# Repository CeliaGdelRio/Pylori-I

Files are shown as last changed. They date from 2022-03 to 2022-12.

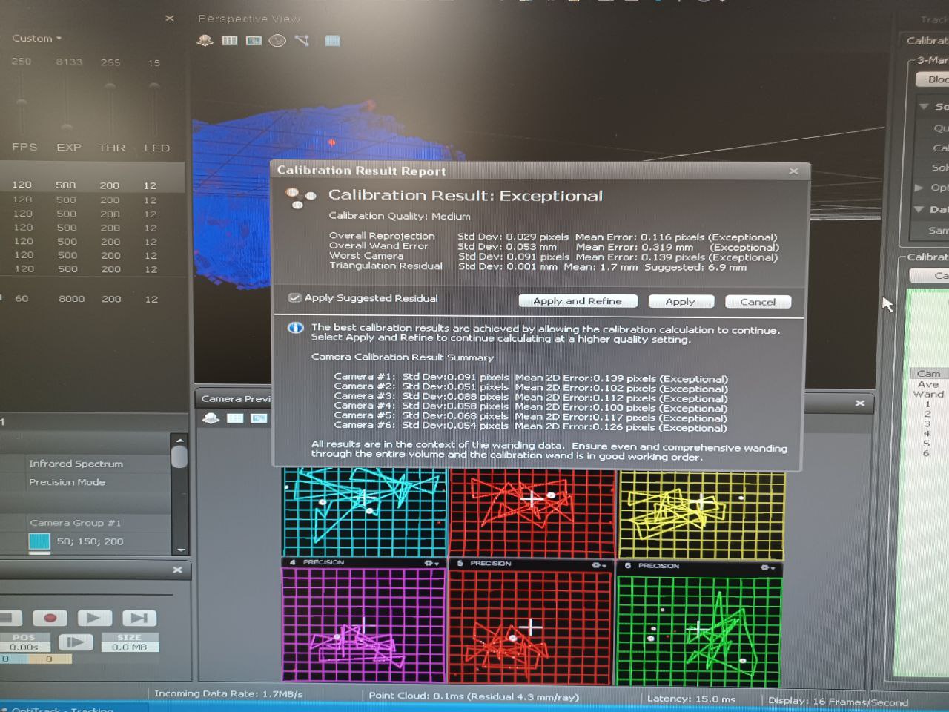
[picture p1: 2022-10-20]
Images/calibracion_final.jpg

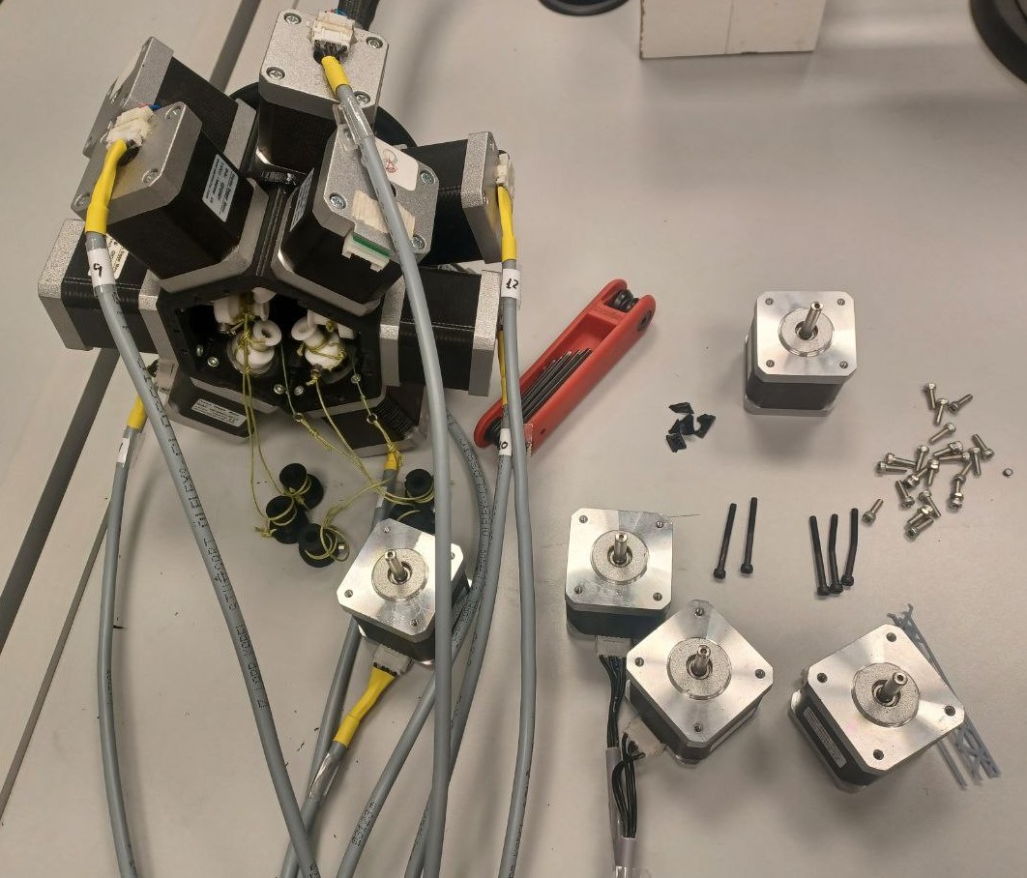
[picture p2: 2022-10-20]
Images/desmontaje.jpg

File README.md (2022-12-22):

# Pylori-I
Hello world!

Este proyecto contiene el código necesario para simular el comportamiento y controlar el movimiento del robot Pylori-I del CAR de la UPM.

Para poder ejecutar este código hay que tener en cuenta varias cosas:
	1. El archivo .ino debe estar cargado en el Arduino Due que contiene el armario. Y de usarse en otro arduino habría además que cargar la librería AccelStepper
	2. El armario debe encenderse correctamente antes de intentar mover el robot: hay que comprobar que el magnetotérmico del interior este subido, la seta de emergencia no esté pulsada y entonces encender el armario.
	3. El código con la cinemática está escrito en MATLAB R2020 o R2021, y el que mueve el robot en MATLAB R2022a, por lo que si se usa en versiones posteriores puede que esté desfasado.
	
### CONTENIDO Y CARPETAS:	

* **Arduino:** Contiene el archivo que debe estar cargado en la placa Arduino Due del armario electrico para poder ejecutar correctamente el código que mueve el robot
* **Images:** Contiene las imagenes que se han empleado para la memoria y algunas mas. Las imagenes que he obtenido de otras fuentes estan debidamente citadas en la memoria TFM_Celia Garijo del Rio.pdf de la carpeta Memorias_TFM. Las demás son de elaboracion propia por lo que se pueden usar citando la memoria (las que aparecen en ella) o este repositorio.
*  **Memorias_TTFM:** Contiene las tres memorias de los trabajos de final de grado o master en los que se ha desarrollado este proyecto.
*  **Red_neuronal:** Contiene el codigo empleado para entrenar las dos redes neuronales en python así como un archivo .csv con los datos que se han empleado en este caso y archivos .txt con las variables (W1, W2, b1, b2, ymin, ymax, xmin y xmax) obtenidas tras entrenar la red que permiten aplicarla en otros programas como Matlab.
*  **Toma de datos:** Contiene el codigo que se ha empleado tanto para la toma de datos del comportamiento del robot como para el tratamiento de datos.
*  **piezas_STL:** Contiene todos los archivos .stl de las piezas mecanicas que se han diseñado para el robot. Para poder ejecutar el codigo que mueve el robot es necesario tener en la misma carpeta los archivos Robot_Base.stl, End_Boro_Triang.stl y Mod_Boro_Triang.stl.

El codigo que queda fuera de las carpetas es el que se emplea para mover el robot y el que contiene la cinematica. A continuacion se describe en mas detalle como usar este ultimo.

### CÓMO SE USA ESTE CÓDIGO:

**IMPORTANTE:** Se ha incluido un archivo .cff en este repositorio para que resulte más sencillo citar este repositorio a quien lo pueda necesitar.

Las funciones Demo y Demo_Trayectorias sirven para simular la cinemática del robot cuando se mueve a un punto (definido en caartesianas), en el caso de Demo, o traza una trayectoria pasando por varios puntos (también en cartesianas), en el caso de Demo_trayectorias; y devuelven los datos necesarios para mover el robot hasta ese punto o trazar esa trayectoria mediante la función moverRobot.
	
**IMPORTANTE:** antes de empezar a ejecutar cualquier función que se comunique con Arduino (moverRobot, calibrarRobot, mover_motor) hay que abrir la conexión con Arduino como se muestra a continuación:
		
```matlab
ardu=serialport("COM3",250000);
```
		
donde "COM3" se deve sustituir por el puerto que esté ocupando Arduino. Y lo primero que hay que hacer después de establecer la conexión es establecer la posición actual como la inicial:
		
```matlab
calibrarRobot(ardu,0,1);
```	
		
Esta conexión no se debe cerrar hasta que no se haya terminado de mover el robot o se perderá los datos sobre cual es la posición inicial. Antes de cerrar se devuelve el robot a la posición inicial y despues se cierra la conexión borrando el objeto ardu:
```matlab
calibrarRobot(ardu,2,1);
delete(ardu);
```

Una vez abierta la conexión y establecida la posición inicial, las formas de mover el robot son las siguientes:
 	
* Para mover motor a motor (mediante la función mover_motor). 
	* Si se quiere mover motor m hasta la posición pos(en pulsos) a la velocidad vel (en pulsos/s):
	```matlab
	mover_motor(ardu,m,2,vel,pos,1);
	```
	* Si se quiere mover motor m a la velocidad vel (en pulsos/s) durante s segundos:
	```matlab
	mover_motor(ardu,m,1,vel,0,s);
	```
* Para moverlo a un punto (x,y,z):
```matlab
[newConfig,error,iter,currentPos]=Demo(x,y,z);
moverRobot(ardu,newConfig,0,1);
```
Donde el 0 en el tercer argumento de moverRobot indica que es un punto y no una trayectoria y el cuarto argumento indica que es un solo punto. Además, la variable error da el error que se espera de la simulación, la variable iter, el nº de iteraciones que ha tenido que hacer la simulación.

* Para llevar el robot a la posición inicial:
```matlab
calibrarRobot(ardu,2,1);
```
* Para establecer la posición actual como la inicial:
```matlab
calibrarRobot(ardu,0,1); 	
```

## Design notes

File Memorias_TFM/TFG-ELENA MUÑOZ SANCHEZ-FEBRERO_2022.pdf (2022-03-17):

# CONSTRUCCIÓN Y CONTROL DE UN ROBOT CONTINUO DE CABLES CON

# DISCOS PIVOTANTES

FEBRERO 2022

# Elena Muñoz Sánchez

DIRECTOR DEL TRABAJO FIN DE GRADO:

## Antonio Barrientos Cruz

## Elena Muñoz Sánchez

### TRABAJO FIN DE GRADOPARA LA OBTENCIÓN DEL TÍTULO DE GRADUADO EN INGENIERÍA EN TECNOLOGÍAS INDUSTRIALES

“Más vale tarde que nunca”

“Algún día diré: No fue fácil, pero lo logré”

ELENA MUÑOZ SÁNCHEZ | V

AGRADECIMIENTOS

En primer lugar, quiero agradecer a mi familia su apoyo y amor incondicional durante estos largos años. Sin vosotros no estaría donde estoy ni habría llegado a ser quien soy ahora.

A mi tutor, Antonio, por creer en mí a lo largo de todo el proyecto más que yo misma, y apoyarme en todas las dudas e impedimentos que me he ido encontrando.

A mis dos grandes mentores, Iván y David, por mostrarme este proyecto y guiarme siempre que lo he necesitado.

A mi compañero Jaime, por ayudarme a materializar el Pylori-I y aguantarme en los peores momentos.

A la asociación de estudiantes RESET, por todo lo que me ha aportado estos últimos años, tanto académica como profesionalmente.

Y a todos los que me habéis acompañado durante esta etapa, en especial a La Taca, a Laura y a Elisa, por compartir esta aventura y levantarme siempre que me caía.

CONSTRUCCIÓN Y CONTROL DE UN ROBOT CONTINUO DE CABLES CON DISCOS PIVOTANTES

ELENA MUÑOZ SÁNCHEZ | VII

RESUMEN

Los robots híper-redundantes son aquellos que poseen un gran número de grados de libertad en comparación con los robots convencionales. La complejidad de su diseño y de su control hacen que su uso no sea tan frecuente como el de los robots no redundantes. Sin embargo, en determinadas aplicaciones, como por ejemplo aquellos casos en los que se hace necesario un elevado grado de maniobrabilidad para trabajar en espacios muy confinados, su uso es casi imprescindible.

El uso de robots híper-redundantes permite resolver con éxito ciertas tareas de inspección o incluso mantenimiento en entornos industriales, aeroespacial, seguridad y vigilancia, y medicina, que serían inabordables con cinemáticas de robots más convencionales.

En este proyecto, se ha diseñado y construido el robot llamado Pylori-I. Se trata de un manipulador continuo híper-redundante que consta de 16 grados de libertad (GdL) distribuidos de cuatro en cuatro a lo largo de sus cuatro secciones. Tiene una longitud de 260 mm a los que se suman otros 48 mm del distribuidor de cables y 155 mm del banco de motores, haciendo un total de 463 mm. La estructura está formada por discos impresos en 3D que pivotan unos sobre otros siguiendo la construcción de robots con twin-pivot compliant joints (TPCJ) y que son accionados mediante motores paso a paso con transmisión por cables.

En su desarrollo, se ha partido del robot desarrollado por Iván Rodríguez en su Trabajo de Fin de Máster [1] y del diseño de endoscopios médicos [2], rediseñando y modificando determinados aspectos para poder llevar a cabo su materialización.

Se trata de un diseño innovador que busca prescindir del empleo del denominado backbone o núcleo central con el que cuentan la mayor parte de los robots híper-redundantes, liberando así el espacio central del robot y aligerando su peso, sin perder sus capacidades de maniobrabilidad que le dotan de gran versatilidad y flexibilidad.

Con este robot se pretende realizar tareas que requieran accesos complicados para el ser humano, como la inspección o el mantenimiento en el interior de máquinas o tuberías, o que sean peligrosas, como la inspección de lugares donde puedan ocultarse explosivos u otro tipo de amenazas. Otra de las principales aplicaciones buscadas, es su empleo en la medicina debido a su pequeño diámetro, lo cual permitiría también realizar inspecciones visuales si se redujera más su tamaño, comportándose como un endoscopio.

Durante el desarrollo del trabajo, se ha realizado un primer estudio del movimiento del robot en Matlab, obteniendo una simulación precisa de su comportamiento. Se han implementado nuevas restricciones, detección de colisiones, cálculo de trayectorias y del espacio de trabajo y estimación de las elongaciones necesarias para los cables. Tras ello, se han rediseñado y fabricado los elementos constitutivos del robot y se ha procedido a su montaje, manteniendo requisitos de posible reconfiguración. Se ha puesto en marcha el sistema de accionamiento basado en motores paso a paso (PaP) y su control mediante Arduino. También se ha diseñado un sistema de calibración y medida buscando facilitar estas tareas habitualmente problemáticas en los robots de cables. Finalmente, se han llevadlo a cabo una serie de experimentos para evaluar la calidad de su posicionamiento.

Los experimentos realizados han permitido obtener una serie de conclusiones y detectar posibles futuras líneas de investigación.

Se espera que este robot suponga un avance en el campo de la robótica híper-redundante y continua que utiliza TPCJ.

RESUMEN

VIII | ESCUELA TÉCNICA SUPERIOR DE INGENIEROS INDUSTRIALES (UPM)

CONSTRUCCIÓN Y CONTROL DE UN ROBOT CONTINUO DE CABLES CON DISCOS PIVOTANTES

ELENA MUÑOZ SÁNCHEZ | IX

ABSTRACT

Hyper-redundant robots are those that have many more degrees of freedom compared to conventional robots. The complexity of its design and control means that its use is not as frequent as that of non-redundant robots, but in certain applications, such as those cases in which a high degree of manoeuvrability is necessary to work in very small spaces, its use is almost essential.

The use of hyper-redundant robots makes it possible to successfully solve certain inspection or even maintenance tasks in industrial, aerospace, security and surveillance, and medical environments, which would be intractable with conventional robot kinematics.

In this project, a robot named Pylori-I has been designed and built. It is a hyper-redundant continuous manipulator consisting of 16 degrees of freedom (DoFs) distributed four by four along its four sections. It has a length of 260 mm to which another 48 mm of the cable distributor and 155 mm of the engine bank are added, making a total of 463 mm. The structure is made up of 3D printed disks that pivot on each other following the construction of robots with twin-pivot compliant joints (TPCJ), and that are driven by stepper motors with cable transmission.

In its development, it has been based on the robot developed by Iván Rodríguez in his master’s Thesis [1] and the design of medical endoscopes [2], redesigning and modifying certain aspects in order to carry out its materialization.

It is an innovative design that seeks to dispense with the use of the so-called backbone or central core that most hyper-redundant robots have, thus freeing up the central space of the robot and lightening its weight, without losing its manoeuvrability capabilities, which give great versatility and flexibility.

This robot is intended to perform tasks that require difficult access for humans, such as inspection or maintenance inside machines or pipes, or that are dangerous, such as inspection of places where explosives or other types of threats may be hidden. Another of the main applications sought is its use in medicine due to its small diameter, which would also allow visual inspections if its size were further reduced, behaving like an endoscope.

During the development of the project, a first study of the robot's movement has been carried out in Matlab, obtaining an accurate simulation of its behaviour. New restrictions, collision detection, calculation of trajectories and workspaces, and estimation of the necessary elongations for the cables have been implemented. Later, the constituent elements of the robot have been redesigned and manufactured and its assembly has proceeded, maintaining the possible reconfiguration requirements. The drive system based on stepper motors (PaP) and its control through Arduino have been launched. A calibration and measurement system has been designed, seeking to facilitate these tasks, which are usually problematic in driven tendons robots. Finally, a series of experiments have been carried out to evaluate the quality of its positioning.

The experiments carried out have made possible to obtain a series of conclusions and to detect possible future lines of research.

This robot is expected to be a breakthrough in the field of hyper-redundant and continuous robotics using TPCJ.

ABSTRACT

X | ESCUELA TÉCNICA SUPERIOR DE INGENIEROS INDUSTRIALES (UPM)

CONSTRUCCIÓN Y CONTROL DE UN ROBOT CONTINUO DE CABLES CON DISCOS PIVOTANTES

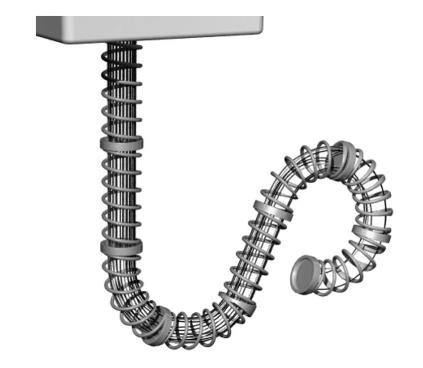
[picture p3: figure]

ELENA MUÑOZ SÁNCHEZ | XI

RESUMEN EJECUTIVO

Actualmente, se puede encontrar una gran variedad de tipos de robots, pero en este trabajo se estudiará el caso del Pylori-I, un robot híper-redundante, continuo y blando construido mediante discos pivotantes y accionado por cables y motores paso a paso.

Un robot híper-redundante es aquel que posee un número de grados de libertad igual o superior al doble del número de dimensiones del espacio de trabajo. De esta manera, este tipo de robots están dotados de una flexibilidad y maniobrabilidad mayores que las de los robots convencionales.

Ilustración 1. Prototipo de robot continuo e híper-redundante. Fuente: http://www.ccad.uiowa.edu/sites/www.ccad.uiowa.edu.vsr/files/files/Continuum-Robot-AR.pdf

Los robots de tipo continuo son aquellos que no están formados por uniones rígidas, lo cual provoca que el robot se deforme de manera continuada y natural, de ahí su nombre.

En el caso de los robots de tipo blando (soft robots), se denominan de esta manera debido a que los materiales que los componen no generan una estructura rígida que pueda causar daños en su entorno. Es por ello por lo que pueden emplearse como robots colaborativos o instrumentos médicos.

A pesar de que una de las funcionalidades principales de los robots híper-redundantes es la inspección visual de zonas poco accesibles, este trabajo se ha centrado en el desarrollo de un robot que se asemeje a un endoscopio y que permita su aplicación en áreas de la cirugía poco invasiva en distintas especialidades médicas y quirúrgicas.

Para el diseño del Pylori-I se han comparado diferentes prototipos estudiados previamente en el Centro de Automática y Robótica, como el Kyma o el MACH-I. Finalmente, se ha decidido implementar el método de construcción que emplea twin-pivot compliant joints.

Para su construcción, se han impreso en 3D la mayor parte de los componentes con la colaboración de la asociación de estudiantes RESET. Los motores e hilos se han tenido que comprar externamente.

RESUMEN EJECUTIVO

XII | ESCUELA TÉCNICA SUPERIOR DE INGENIEROS INDUSTRIALES (UPM)

Para la colocación del robot en posición horizontal, se ha diseñado un soporte ad hoc adaptado a los espacios libres que dejan los motores.

Ilustración 2. Pylori-I conectado al armario eléctrico y colocado horizontalmente sobre el soporte

La actuación mediante cables se ha dividido en dos fases que utilizan un tipo de cable diferente. Aunque ambos son hilos de pesca, el más grueso se colocará en la polea, ya que va a ser el cable que más sufra de los dos, enrollándose y desarrollándose continuamente. Además, el banco de motores es extrínseco al cuerpo del robot, por lo que aligerará en gran medida el peso del brazo robótico.

Ilustración 3. Cables usados para la actuación. Fuente: https://www.amazon.es/

En cuanto a la construcción del brazo robótico, la estructura está formada por apilamientos de discos que forman secciones siguiendo una distribución 20-12-12-8 partiendo desde la base.

Cada una de las secciones tiene como disco final una modificación de los anteriores para poder alojar el final de los cables en su cara lateral. Además, estas secciones se encuentran desfasadas 2π/16 radianes entre sí y están actuadas cada una de ellas por cuatro cables diametralmente opuestos dos a dos.

Esta configuración de los cables ha sido estudiada en el trabajo, resultando ser la que menores tensiones genera.

CONSTRUCCIÓN Y CONTROL DE UN ROBOT CONTINUO DE CABLES CON DISCOS PIVOTANTES

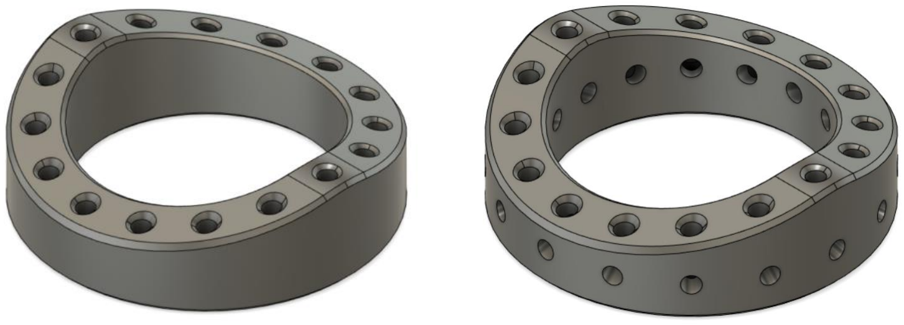
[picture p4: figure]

ELENA MUÑOZ SÁNCHEZ | XIII

Ilustración 4. Discos utilizados en la construcción de las secciones

En total, se obtienen 16 grados de libertad para todo el robot, cuatro por sección, quedando como diseño final el siguiente:

Ilustración 5. Diseño final del Pylori-I realizado con Catia V5

En cuanto al control cinemático del robot, se ha hecho un estudio y comparación de tres cinemáticas existentes, descartando aquellas que utilizan el método de cálculo de la matriz Jacobiana.

Una vez determinado cómo se va a generar el movimiento del Pylori-I, se han implementado nuevos métodos y funciones en Matlab que serán utilizados para el posicionamiento del extremo, la generación de trayectorias, la detección de colisiones, el cálculo de las elongaciones de cada uno de los cables y la estimación de las dimensiones del espacio de trabajo.

También mediante Matlab, se ha creado una interfaz hombre-máquina dentro de la cual se podrá activar la conexión Matlab-Arduino, ver el número total de colisiones ocasionadas y los discos implicados en las mismas y, lo más importante, introducir coordenadas que generen la simulación de posicionamiento del extremo.

Esta interfaz también mostrará la posición real en la que se ha situado el Tool Center Point y el error generado en el posicionamiento.

RESUMEN EJECUTIVO

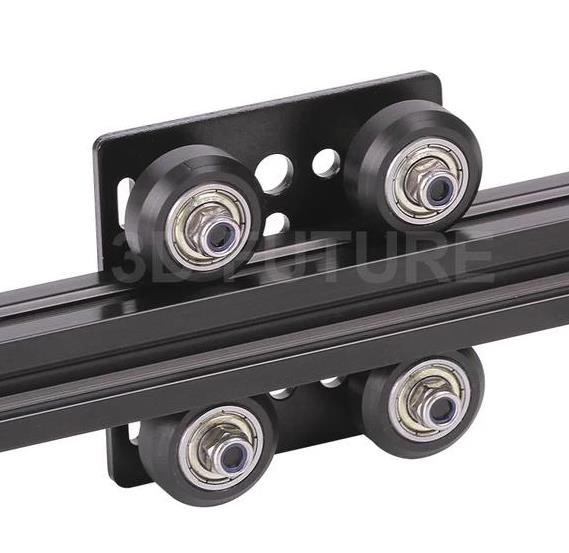
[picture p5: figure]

XIV | ESCUELA TÉCNICA SUPERIOR DE INGENIEROS INDUSTRIALES (UPM)

Ilustración 6. Pantalla principal de la interfaz

En lo referido al hardware de control, se han utilizado motores paso a paso NEMA17 cuyo conexionado se ha realizado a través de un armario eléctrico proporcionado por el Centro de Automática y Robótica.

Este armario está compuesto por 18 drivers de tipo TB6600 y un Arduino Due. Las dos conexiones sobrantes del armario permitirán en un futuro conectar motores que se encarguen del manejo de una herramienta colocada en el extremo del robot.

Los drivers están configurados para que cada motor de 200 pasos/rev tenga un microstepping que los transforme en 1600 pulsos por revolución.

Una vez iniciado el puerto Serial de Arduino, se enviarán a la placa los pulsos calculados por Matlab para cada uno de los motores siguiendo esta sintaxis:

[Motor;Comando;Arg1;Arg2;]

Para la realización de experimentos se ha construido un espacio físico de trabajo para poder realizar medidas de calibración y de posicionamiento.

El conjunto del espacio de trabajo está formado por perfiles de aluminio, carros V-Slot, piezas impresas en 3D y láseres.

Ilustración 7. Ejemplo de carro V-Slot

CONSTRUCCIÓN Y CONTROL DE UN ROBOT CONTINUO DE CABLES CON DISCOS PIVOTANTES

ELENA MUÑOZ SÁNCHEZ | XV

La calibración del robot se realiza a través de Matlab con la siguiente función en los modos ‘0’ y ‘1’:

function calibrarArduino(Arduino,modo,motor,pul);

El modo ‘0’ guarda la posición actual de cada uno de los motores como la posición de reposo. El modo ‘1’ sirve para enviar un número de pulsos a un motor concreto, realizando de esta manera, poco a poco, una calibración de cada uno de los motores hasta que el robot se encuentre alineado con los láseres lineares fijos de los perfiles.

Los experimentos realizados se han centrado en la medición de las coordenadas de la posición final del extremo del robot calculada de forma directa o mediante la generación de una trayectoria. Además, se han generado trayectorias con diferente número de puntos intermedios para enriquecer el estudio y la discusión posterior.

Una vez analizados los datos obtenidos, se puede concluir que el error de posicionamiento producido en la generación de trayectorias es menor que en el posicionamiento directo. Sin embargo, no se aprecia una influencia significativa del número de puntos intermedios de las trayectorias.

Como posibles futuras líneas de investigación para este proyecto se han propuesto la mejora de la interfaz, la reconstrucción con materiales más fiables y que generen menos rozamiento, la instalación de una herramienta en el extremo del robot, ya sea una pinza o una cámara para inspección, el diseño de un método de calibración y de medición más fiable y preciso, y la implementación de un control mediante joystick o realidad virtual.

La conclusión principal obtenida de la realización de este proyecto es que se observan diferencias entre el comportamiento del robot físico y los obtenidos de manera teórica, lo cual puede deberse a que se ha considerado un comportamiento ideal para el robot (la flexión de la sección se distribuye uniformemente a lo largo de todos los discos que la conforman), a la fricción entre cables y discos, a una mala calibración inicial o a la pérdida de ésta según se avanza con las pruebas.
Sin embargo, hay que destacar que el comportamiento del robot no es del todo erróneo ya que se orienta y aproxima hacia el punto deseado y, pese a que se trata del primer prototipo realizado en el Centro de Automática y Robótica que emplea twin-pivot compliant joints como método constructivo, el Pylori-I posee todas las características buscadas para tener una gran flexibilidad y maniobrabilidad.

Información accesible:

Repositorio:
https://github.com/LnaMzSz/Pylori-I
Lista de reproducción:
https://youtube.com/playlist?list=PL3Q5Xz4yvA3jVhCCdIYIbSSO-qLm97V_n

Palabras clave:

Automática, automatización, continuo, control, híper-redundante, manipulador, robot, robótica, simulación.

RESUMEN EJECUTIVO

XVI | ESCUELA TÉCNICA SUPERIOR DE INGENIEROS INDUSTRIALES (UPM)

Códigos UNESCO:

120326 – Simulación

330491 – Robótica

331101 – Tecnología de la automatización

331102 – Ingeniería de control

CONSTRUCCIÓN Y CONTROL DE UN ROBOT CONTINUO DE CABLES CON DISCOS PIVOTANTES

ELENA MUÑOZ SÁNCHEZ | XVII

ÍNDICE DE CONTENIDOS

AGRADECIMIENTOS | V
RESUMEN | VII
ABSTRACT | IX
RESUMEN EJECUTIVO | XI
ÍNDICE DE CONTENIDOS | XVII
ÍNDICE DE FIGURAS | XIX
ÍNDICE DE TABLAS | XXI

ÍNDICE DE CONTENIDOS

XVIII | ESCUELA TÉCNICA SUPERIOR DE INGENIEROS INDUSTRIALES (UPM)

CONSTRUCCIÓN Y CONTROL DE UN ROBOT CONTINUO DE CABLES CON DISCOS PIVOTANTES

ELENA MUÑOZ SÁNCHEZ | XIX

ÍNDICE DE FIGURAS

Ilustración 1. Prototipo de robot continuo e híper-redundante. Fuente:
http://www.ccad.uiowa.edu/sites/www.ccad.uiowa.edu.vsr/files/files/Continuum-Robot-AR.pdf | XI
Ilustración 2. Pyltori-I conectado al armario eléctrico y colocado horizontalmente sobre el soporte .... XII
Ilustración 3. Cables usados para la actuación. Fuente: https://www.amazon.es/ | XII
Ilustración 4. Discos utilizados en la construcción de las secciones | XIII
Ilustración 5. Diseño final del Pylori-I realizado con Catia V5 | XIII
Ilustración 6. Pantalla principal de la interfaz | XIV
Ilustración 7. Ejemplo de carro V-Slot | XIV
Ilustración 8. Ejemplo de robot continuo construido mediante twin-pivot compliant joints. Fuente: [3] .. 1

Ilustración 11. Representación en función de su número de GdL en un espacio tridimensional (m=3).
(a) Robot no redundante de tipo n<m. (b) Robot no redundante de tipo n=m. (c) Robot redundante de

Ilustración 12. Ejemplo de robot manipulador móvil. Fuente:

Ilustración 14. Ejemplo de representación de un robot continuo accionado mediante cables. Fuente:

Ilustración 17. Esquema de la construcción de robots continuos. En el caso del uso de TPCJ (a), los

Ilustración 18. Parámetros de la cinemática de robots continuos con backbone y TPCJ. Fuente: [12] 11

Ilustración 20. Robot concéntrico compuesto de un tubo exterior y un tubo guía que alberga la fibra

Ilustración 21. (A) Sistema de robot continuo tubular para cirugía de laringe. (B) Modelo de laringe

Ilustración 26. Bacteria Helicobacter Pylori y robot Pylori-I. Fuente:

Ilustración 36. Bobina de Nylon PA12 Blanco. Fuente: https://www.3djake.es/fiberlogy/nylon-pa12-

Ilustración 40. Malla cubre cables. Fuente: https://computacion.mercadolibre.com.ar/cables-hubs-

ÍNDICE DE FIGURAS

XX | ESCUELA TÉCNICA SUPERIOR DE INGENIEROS INDUSTRIALES (UPM)

Ilustración 45. A la izquierda, Método de la Jacobiana utilizando como variables los ángulos de los discos. A la derecha, Método de la Jacobiana utilizando como variables los ángulos de las secciones

Ilustración 46. Posición real del extremo y error generado con el Método del Descenso del Gradiente.

Ilustración 49. Representación de los ángulos θ, φ y α de la sección. Fuente: Modificado de [17] ...... 32

Ilustración 62. Visión general del espacio de trabajo y posicionamiento del Pylori-I en el mismo ........ 43

CONSTRUCCIÓN Y CONTROL DE UN ROBOT CONTINUO DE CABLES CON DISCOS PIVOTANTES

ELENA MUÑOZ SÁNCHEZ | XXI

ÍNDICE DE TABLAS

ÍNDICE DE TABLAS

XXII | ESCUELA TÉCNICA SUPERIOR DE INGENIEROS INDUSTRIALES (UPM)

# 1. INTRODUCCIÓN

CONSTRUCCIÓN Y CONTROL DE UN ROBOT CONTINUO DE CABLES CON DISCOS PIVOTANTES

ELENA MUÑOZ SÁNCHEZ | 1

### 1. INTRODUCCIÓN

### 1.1. Motivación

La principal motivación para la realización de este proyecto es que se trata de un gran reto tanto mecánico como automático, dada la innovación y la dedicación necesaria.

Ilustración 8. Ejemplo de robot continuo construido mediante twin-pivot compliant joints. Fuente: [3]

Pese a la idea previa de que, quizás, tras su realización, acabara siendo un proyecto poco viable o no funcionara de manera correcta fuera de la simulación por tratarse de un primer prototipo, la posibilidad de adentrarse de esta manera en el campo de la robótica y poner en práctica todos los conocimientos adquiridos durante estos últimos años fue suficiente para seguir adelante.

Por último, ser partícipe de un proyecto tan amplio que involucra tantos campos de la ingeniería y tantas líneas futuras diferentes de investigación y de mejora, ha supuesto adquirir unos conocimientos que, realizando un proyecto más común y conocido, no habría sido posible obtener.

1.1.1. Motivación personal

Por otro lado, la motivación personal que me ha llevado hasta aquí ha sido lo atractiva que era la idea de construir y controlar un tipo de robot diferente de los que ya se han estudiado en otros trabajos de fin de carrera o máster en el Centro de Automática y Robótica (CAR).

También es un orgullo poder retomar un proyecto ideado por un amigo y antiguo alumno y hacerlo real, además de su desarrollo en simulación.

### 1.2. Objetivos

Los objetivos del proyecto se pueden dividir en tres partes:

En primer lugar, realizar un estudio del estado del arte de robots híper-redundantes, e investigar y adquirir los conocimientos necesarios para la adaptación del diseño original y su posterior construcción y control. En concreto, se ha decidido abarcar la posible mejora que puede suponer un robot híper-redundante que no posea un eje flexible central y que sea de tamaño muy reducido.

Para rediseñar los componentes existentes y crear nuevos, será necesario familiarizarse con el uso de programas tanto de diseño 3D, concretamente Catia V5 y Autodesk Fusion 360; como de impresión 3D, Simplify 3D y Prusa Slicer.

INTRODUCCIÓN

2 | ESCUELA TÉCNICA SUPERIOR DE INGENIEROS INDUSTRIALES (UPM)

En segundo lugar, se encuentra el estudio de las cinemáticas existentes del robot mediante Matlab. Para ello, se emplea una simulación que permite contemplar el comportamiento del robot en tres dimensiones dentro de su espacio de trabajo. Además, se añaden nuevas restricciones, así como la detección de colisiones, el cálculo de trayectorias y del espacio de trabajo, la estimación de las elongaciones de los cables y la comunicación Matlab-Arduino.

En tercer y último lugar, se procede con la construcción del robot, el estudio del armario eléctrico proporcionado por el CAR, la realización del control mediante Arduino, y la realización de los experimentos de comprobación del funcionamiento.

Además de todo lo mencionado, se pretende aprender a realizar un Trabajo de Fin de Grado, con la correspondiente adquisición de nuevos conocimientos y capacidades como la planificación temporal o el estudio económico de un proyecto.

### 1.3. Estructura del proyecto

A continuación, se realiza un breve resumen por capítulos de todo el trabajo, excluyendo el capítulo actual, Cap. 1: INTRODUCCIÓN, en el que se han explicado la motivación, los diferentes objetivos buscados, y la siguiente estructura:

- Cap. 2: ESTADO DEL ARTE
Se explicara qué son los robots híper-redundantes, sus principales características, sus clasificaciones, los diferentes tipos de construcción y su similitud con los endoscopios utilizados en medicina.
- Cap. 3: DISEÑO MECÁNICO Y CONSTRUCCIÓN

En este capítulo se realizará una comparación de prototipos y se mostrará el diseño final elegido. Se explicarán las diferentes partes que componen al robot, los rediseños de componentes necesarios y la posterior construcción.
- Cap. 4: CONTROL DE MOVIMIENTO DEL PYLORI-I
En este capítulo se estudiarán las diferentes cinemáticas existentes y se explicarán las funcionalidades programadas para el robot.
- Cap. 5: HARDWARE DE CONTROL
Se hará una descripción de los componentes del armario eléctrico, así como del control realizado con Arduino.
- Cap. 6: EXPERIMENTOS Y RESULTADOS
Se explicará la puesta en marcha del robot, se expondrán los resultados de los experimentos realizados, y se discutirán los posibles fallos y mejoras.
- Cap. 7: LÍNEAS FUTURAS

Tras la discusión de los resultados obtenidos, se estudiarán las posibles mejoras futuras y las nuevas líneas de investigación que se podrían seguir de aquí en adelante.

- Cap. 8: CONCLUSIONES
Una vez realizados los capítulos anteriores, se resumirán en este último todas las conclusiones, tanto positivas como negativas, a las que se haya llegado a lo largo del proyecto.
- ANEXO I: GLOSARIO Y ABREVIATURAS
Se incluirán las definiciones y abreviaturas de las palabras clave del proyecto.

CONSTRUCCIÓN Y CONTROL DE UN ROBOT CONTINUO DE CABLES CON DISCOS PIVOTANTES

ELENA MUÑOZ SÁNCHEZ | 3
- ANEXO II: IMPACTO SOCIAL, AMBIENTAL Y ECONÓMICO

En este anexo, se expondrá un breve estudio del impacto que este proyecto puede llegar a producir en el mundo, tanto medioambientalmente como de manera social y económica.
- ANEXO III: PLANIFICACIÓN TEMPORAL

Se mostrará la planificación temporal a través de un diagrama de Gantt y una Estructura de Descomposición del Proyecto (EDP).
- ANEXO IV: ESTUDIO ECONÓMICO

Por último, se realizará un estudio de los costes totales que ha supuesto la realización de este proyecto.

INTRODUCCIÓN

4 | ESCUELA TÉCNICA SUPERIOR DE INGENIEROS INDUSTRIALES (UPM)

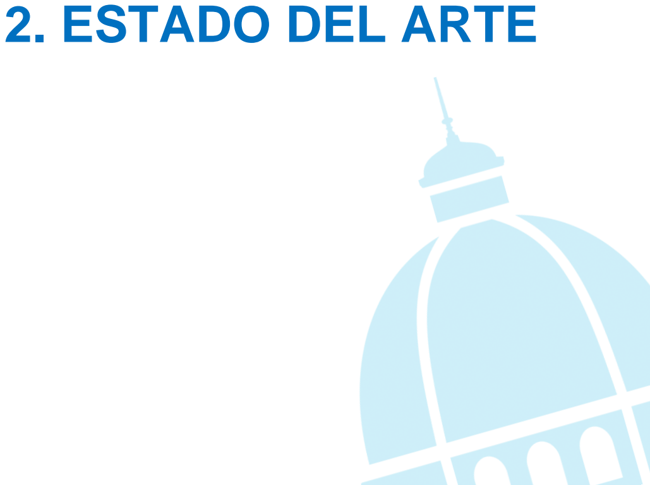
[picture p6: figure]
2. ESTADO DEL ARTE

CONSTRUCCIÓN Y CONTROL DE UN ROBOT CONTINUO DE CABLES CON DISCOS PIVOTANTES

ELENA MUÑOZ SÁNCHEZ | 5

### 2. ESTADO DEL ARTE

### 2.1. Los robots

Existen diferentes definiciones para lo que se conoce como “robot”. Por ejemplo, puede referirse a un objeto que imita comportamientos de un ser animado, una persona que actúa de manera mecánica, o una máquina programable que es capaz de manipular objetos y realizar diferentes tareas.[4] Para este proyecto, la definición más adecuada es la última mencionada.

Por otro lado, el término "híper-redundante", al cual se hará mención muy frecuentemente a lo largo del documento, se refiere a manipuladores con un número muy grande de grados de libertad en comparación con los robots más comunes. Además, se trata de robots que se asemejan bastante a
serpientes, | gusanos, | trompas | de
elefante o tentáculos. [5]

Aunque el proyecto trata de un robot híper-redundante, se va a hacer un estudio de la clasificación general de los robots para más adelante profundizar en el sector que concierne a este trabajo.

### 2.2. Clasificación de los robots

Los robots pueden clasificarse siguiendo cinco características diferentes: según su número de grados de libertad (GdL), según su número de articulaciones, según su funcionalidad, según los materiales con los que se ha construido, y según el tipo de actuación empleada.

Ilustración 10. Diagrama de Venn para la clasificación de los robots. Fuente: [6]

Ilustración 9. Ejemplo de snake-robot. Fuente: https://www.reset.etsii.upm.es/

ESTADO DEL ARTE

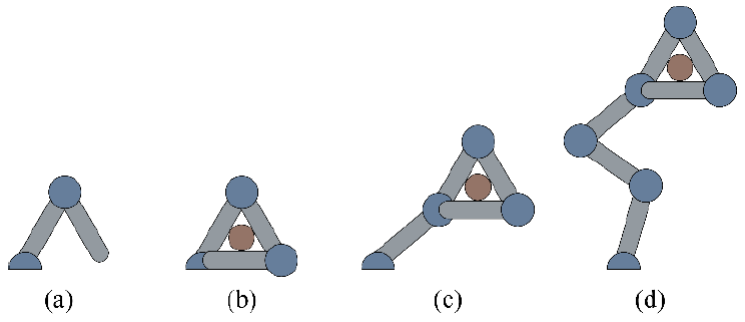
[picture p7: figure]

6 | ESCUELA TÉCNICA SUPERIOR DE INGENIEROS INDUSTRIALES (UPM)
- Según el número de GdL
El número de GdL de un robot es el número de coordenadas independientes que son necesarias para posicionar su extremo respecto a un sistema de referencia dado. [7]

Dentro de esta clasificación se pueden distinguir tres tipos diferentes de robots: no redundantes, redundantes e híper-redundantes.

Siendo m las dimensiones del espacio de trabajo del robot, el número de GdL mínimos necesarios para posicionar su extremo viene dado por la siguiente expresión:

n =

m ∙ (m + 1)
2

De esta manera, se clasificarán como no redundantes aquellos que tengan un número de GdL menor o igual al mínimo necesario; como redundantes aquellos con un número de GdL mayor que el necesario; y como híper-redundantes aquellos que tengan al menos el doble de GdL necesarios.

Ilustración 11. Representación en función de su número de GdL en un espacio tridimensional (m=3). (a) Robot no redundante de tipo n<m. (b) Robot no redundante de tipo n=m. (c) Robot redundante de tipo n>m. (d) Robot híper-redundante de tipo n=2m. Fuente: [6]

- Según el número de articulaciones
Hay que destacar que el término “articulación” no es el mismo que el término “GdL”. Una articulación consiste en una unión entre dos piezas rígidas que permite el movimiento relativo entre ellas. [4]

A su vez, en esta otra clasificación, se diferenciará entre robots continuos y robots discretos.

Los primeros son aquellos que no están formados por uniones rígidas sino por una estructura en la que un único actuador puede transmitir movimiento a más de un eje. Esto provoca que el robot se deforme de manera continuada y natural, de ahí su nombre.

Por otro lado, se denominan robots discretos a aquellos construidos mediante uniones rígidas y perfectamente distinguibles.

- Según su funcionalidad
Atendiendo a la funcionalidad que se tiene como objetivo para el robot, se encuentran dos posibles tipos de robot: manipuladores y móviles.

CONSTRUCCIÓN Y CONTROL DE UN ROBOT CONTINUO DE CABLES CON DISCOS PIVOTANTES

ELENA MUÑOZ SÁNCHEZ | 7

Los robots manipuladores buscan precisión en el posicionamiento del extremo para poder emplear una herramienta que manipule objetos. Además, suelen encontrarse en un espacio de trabajo fijo dentro del cual no se desplazan.

Sin embargo, los robots móviles tienen la capacidad de moverse de un lugar a otro, no teniendo un espacio de trabajo definido.

Cabe la posibilidad de encontrar una mezcla de ambos tipos, los llamados robots híbridos. Estos robots son manipuladores situados en bases móviles, dotando así de locomoción a los primeros. [6]

Ilustración 12. Ejemplo de robot manipulador móvil. Fuente: https://robotnik.eu/es/productos/manipuladores-moviles/

- Según los materiales de construcción
Teniendo en cuenta los materiales utilizados
en la construcción del robot, se diferenciará entre robots duros y robots blandos.

Los robots duros (hard robots) están constituidos por articulaciones rígidas, tratándose así de robots no redundantes generalmente. Por otro lado, los robots blandos (soft robots) tienen una gran adaptación al entorno que les permite sortear objetos con facilidad y pueden ser usados como robots colaborativos dado que están compuestos por materiales blandos que no causarían grandes daños en caso de colisión con una persona. [8]

Como se puede apreciar en la Ilustración 10, los robots de tipo blando están englobados dentro de los robots híper-redundantes y continuos.

- Según el tipo de actuación
Para conseguir un movimiento a lo largo de la estructura del robot, es necesario tener un método de actuación para las articulaciones. Los más utilizados en el caso de robots híper-

Ilustración 13. Ejemplo de robot blando. OctArm VI. Fuente: [6]

ESTADO DEL ARTE

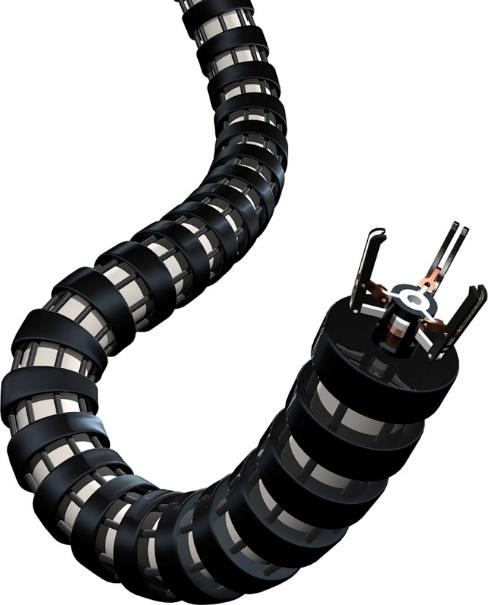
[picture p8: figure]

8 | ESCUELA TÉCNICA SUPERIOR DE INGENIEROS INDUSTRIALES (UPM)

redundantes son el accionamiento mediante cables, las articulaciones motorizadas y la actuación neumática. [1]

El accionamiento por cables permite transferir movimiento a zonas concretas del robot mediante la aplicación de tensión, dotando a la estructura de un movimiento continuo y natural.

Para generar dicha tensión, se emplean motores eléctricos situados en una base extrínseca al brazo robótico, lo cual permite reducir en gran cantidad el peso de éste.

Por otro lado, las articulaciones motorizadas sí forman parte del cuerpo del robot ya que, por lo general, los motores se colocan en las propias articulaciones. Se evita la utilización de elementos de actuación, pero se incrementa en gran medida el peso del robot, lo cual no resulta viable para la construcción.

Por último, hay que destacar que la actuación neumática tiene muchas aplicaciones y es comúnmente utilizada en robots blandos debido a que el aire comprimido no proporciona una estructura rígida por completo. Al igual que en la actuación por cables, se trabaja de forma extrínseca al brazo robótico, pero la dificultad de control es mayor a causa de la regulación de las presiones.

La actuación por cables y por aire comprimido son las más empleadas en robots híper-redundantes, como ya se ha mencionado, debido a sus numerosas ventajas: reducción del peso del robot, trabajo de manera extrínseca, dotación de un movimiento continuo y natural, semejanza con elementos biológicos que evita impactos ambientales, y posibilidad de funcionar como robots colaborativos.

### 2.3. Robots híper-redundantes actuados mediante cables

Como ya se ha mencionado anteriormente, el Pylori-I es un robot híper-redundante continuo actuado mediante cables y motores paso a paso (PaP). Como referencia de estudio, se han tenido soluciones anteriores realizadas en el CAR y que han servido para fijar los objetivos de este trabajo.

Ilustración 14. Ejemplo de representación de un robot continuo accionado mediante cables. Fuente: [2]

La actuación mediante cables es uno de los principios de actuación más destacados para los robots continuos como ya se ha comentado anteriormente. Hasta la fecha, se ha derivado una amplia variedad de enfoques de modelado para describir las deformaciones de los robots continuos accionados por cables.

CONSTRUCCIÓN Y CONTROL DE UN ROBOT CONTINUO DE CABLES CON DISCOS PIVOTANTES

ELENA MUÑOZ SÁNCHEZ | 9
2.3.1. Soluciones previas en el CAR
- Kyma
Consiste en un robot de tipo blando y continuo desarrollado por Cecilia Martínez en 2017 [9]. Está construido con fuelles que proporcionan tres GdL por sección, con un total de cuatro secciones.

Ilustración 15. Robot Kyma (‘onda’ en griego). Fuente: [9]

El accionamiento de este robot se realiza mediante cables y motores PaP conectados entre sí mediante poleas.

- MACH-I
Se trata de un robot inspirado en la trompa de un elefante. Fue diseñado y desarrollado inicialmente por Iván Rodríguez en 2019 [1] y continuado más adelante por David Márquez en 2021 [10].

Es un robot híper-redundante actuado por cables, pero al contrario que ocurría con el robot Kyma, el MACH-I se clasifica como robot duro y discreto.

Ilustración 16. Robot MACH-I. Fuente: [10]

ESTADO DEL ARTE

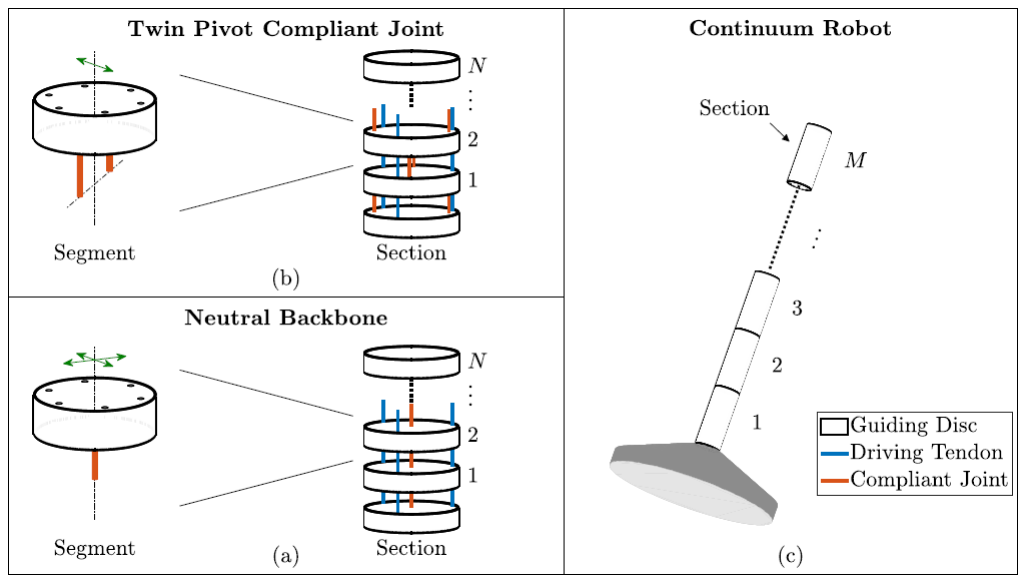
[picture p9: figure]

10 | ESCUELA TÉCNICA SUPERIOR DE INGENIEROS INDUSTRIALES (UPM)

Consta de siete articulaciones con dos GdL por cada una, lo que le confiere su cualidad de robot híper-redundante. Además, cuenta con tres GdL adicionales para actuar sobre una herramienta situada en su extremo.

2.3.2. Backbone vs. twin-pivot complaint joints

En este proyecto, se va a profundizar en la utilización de pivotes en las uniones en lugar de la unión mediante eje flexible o rótulas, lo cual se considera una innovación debido a que no se ha desarrollado ningún robot de este tipo previamente en el CAR. A continuación, se hace un breve estudio y comparación de la información que se tiene respecto a ambas soluciones.

La unidad básica de un robot continuo accionado por cables es el denominado “segmento”. Un segmento es en un componente rígido, llamado disco, junto con un cuerpo elástico, conocido como backbone. [11]

El objetivo de cada uno de los discos que componen la estructura es guiar los cables a través de ésta hasta el extremo de la sección correspondiente, y actuar como limitación de movimiento de la backbone.

Por otro lado, la función del eje flexible (backbone) es dotar al robot de la capacidad de adaptación a diferentes posiciones.

El método utilizado más comúnmente es aquel que utiliza un eje flexible colocado en el eje neutral de los discos del brazo robótico, pero conlleva un gran inconveniente a largo plazo. Este eje flexible tiende a sufrir deformaciones, lo cual provoca la pérdida de control de movimientos de los sectores finales.

Para resolver dicha desventaja, los robots que emplean twin-pivot complaint joints (TPCJ) cambian el diseño de una backbone por dos elementos elásticos diametralmente opuestos. Esta modificación aporta mayor rigidez torsional y libera el eje central para un posible paso de cables para la conexión de una herramienta en el Tool Center Point (TCP). [12]

El montaje que emplea TPCJ, a diferencia de lo que ocurre con un eje flexible, limita los GdL del segmento a uno solo, siendo el eje de flexión del disco el perpendicular al generado por los dos pivotes.

Ilustración 17. Esquema de la construcción de robots continuos. En el caso del uso de TPCJ (a), los segmentos están desfasados alternativamente π/2. Fuente: [12]

CONSTRUCCIÓN Y CONTROL DE UN ROBOT CONTINUO DE CABLES CON DISCOS PIVOTANTES

ELENA MUÑOZ SÁNCHEZ | 11

Una vez apilados N discos, se obtiene la denominada “sección” de un robot. Cada sección está actuada por tres o cuatro cables generalmente, en el caso del Pylori-I, se utilizarán cuatro cables actuadores.

Cada uno de los discos pertenecientes a una sección están vinculados cinéticamente entre sí y actuados por los mismos cables. De manera ideal, que es la que se ha considerado en el desarrollo de este proyecto, la flexión de la sección se distribuirá uniformemente a lo largo de todos los discos que la conforman.

Cabe destacar que el número total de GdL del robot en el caso de utilización de TPCJ, viene dado por el apilamiento de discos con un solo GdL desfasados π/2 entre sí, de tal forma que se obtengan dos GdL por sección, asemejándose así al uso de backbone.

Ilustración 18. Parámetros de la cinemática de robots continuos con backbone y TPCJ. Fuente: [12]

Por último, llegada la hora de la construcción del prototipo, se ha de tener en cuenta que los actuadores de las últimas secciones tienen que pasar a través de las anteriores. Como los cables de las últimas secciones no pueden pasar por las mismas guías que los anteriores, la solución es un desplazamiento angular δ en torno al eje central de los discos para cada sección.

### 2.4. El endoscopio

Los robots continuos son delgados y blandos, y se caracterizan por su alta flexibilidad y su fácil miniaturización. Estas ventajas de las que disponen permiten su aplicación en áreas como la inspección o la cirugía poco invasiva en distintas especialidades médicas y quirúrgicas (neumología, otorrinolaringología, cardiología, aparato digestivo, cirugía general y neurocirugía entre otras). [2]

El endoscopio es un dispositivo médico con una luz incluida creado para poder adentrarse dentro de una cavidad u órgano corporal y observarla. Los procedimientos médicos que utilizan estos instrumentos se denominan “endoscopias”. [13]

2.4.1. Endoscopios robotizados

A continuación, se van a exponer diferentes escenarios en los que se han empleado robots similares al Pylori-I que han sido desarrollados hasta el punto de aplicación en áreas médicas del día a día.

En el área de la neumología, este tipo de robots se han empleado en la toma de muestras de tejido pulmonar a través de bronquios distales de pequeño calibre. [14] Cuanto mayor es la miniaturización de estos endoscopios robotizados, menor será el calibre de los bronquios a los que se puede llegar a acceder con ellos.

ESTADO DEL ARTE

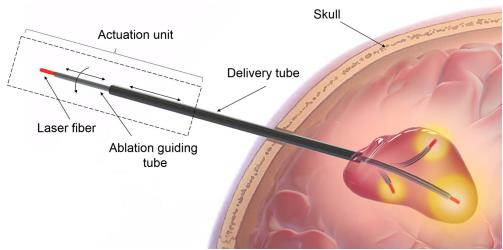
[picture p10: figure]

12 | ESCUELA TÉCNICA SUPERIOR DE INGENIEROS INDUSTRIALES (UPM)

Ilustración 19. Esquema de broncoscopia pulmonar. Fuente: [14]

Este tipo de muestreo pulmonar en pacientes con enfermedades pulmonares como la COVID-19 no está estandarizado, carece de reproducibilidad y requiere operadores expertos. Para ello se propone este tipo de endoscopio (broncoscopio) robotizado que supera los desafíos más importantes a la hora de realizar una broncoscopia, como pueden ser la destreza limitada o el gran tamaño de un broncoscopio convencional. [14]

Dentro del área de la neurocirugía, se puede destacar la termoterapia inducida por láser en el cerebro. Se trata de un procedimiento mínimamente invasivo para acabar con el tejido tumoral.

Dado que los tumores cerebrales de forma irregular no pueden tratarse utilizando los sistemas existentes, se ha presentado un sistema robótico de tubos concéntricos para el tratamiento de éstos. [15]

Ilustración 20. Robot concéntrico compuesto de un tubo exterior y un tubo guía que alberga la fibra láser (roja). Fuente: [15]

CONSTRUCCIÓN Y CONTROL DE UN ROBOT CONTINUO DE CABLES CON DISCOS PIVOTANTES

ELENA MUÑOZ SÁNCHEZ | 13

Por último, en el caso de la otorrinolaringología, se han realizado estudios en modelos de laringes porcinas para evaluar la factibilidad de cirugías transorales con este tipo de robot teleoperado. [16]

La cirugía transoral asistida por robot es cada vez más común lo que conlleva grandes avances en esta área. Sin embargo, los sistemas actuales son incapaces de profundizar lo suficiente como para alcanzar áreas subglóticas.

Ilustración 21. (A) Sistema de robot continuo tubular para cirugía de laringe. (B) Modelo de laringe porcina siendo visualizado mediante endoscopia. Fuente: [16]

ESTADO DEL ARTE

14 | ESCUELA TÉCNICA SUPERIOR DE INGENIEROS INDUSTRIALES (UPM)

# 3. DISEÑO MECÁNICO Y

CONSTRUCCIÓN Y CONTROL DE UN ROBOT CONTINUO DE CABLES CON DISCOS PIVOTANTES

ELENA MUÑOZ SÁNCHEZ | 15

### 3. DISEÑO MECÁNICO Y CONSTRUCCIÓN

### 3.1. Generalidades

Como objetivo principal, se quiere diseñar un robot híper-redundante accionado mediante cables partiendo de las experiencias anteriores en el CAR con robots como Kyma y MACH-I, pero buscando un tipo diferente de robot. De manera más concreta, el objetivo es diseñar y construir un robot de menor escala que los mencionados y que, además, no utilice juntas rígidas ni un eje flexible central. De esta manera, se ganará accesibilidad a espacios más estrechos o de difícil inspección.

Además, se desea que la base del robot pueda usarse con diferentes prototipos, por lo que ha de ser un diseño estándar, generalizado y fácilmente desmontable.

Por último, dado que se trata de un primer montaje de un prototipo para su estudio, no es necesario que el robot sea duradero en el tiempo. Por lo que los componentes del robot, tanto del brazo robótico como de la base de motores, se van a fabricar por impresión 3D. De esta manera, se espera que se minimicen los costes dentro de lo posible.

### 3.2. Requisitos del brazo robótico

3.2.1. Sección y longitud

Ambas dimensiones son críticas para el diseño, pues de ellas dependerá el espacio de trabajo del robot. Dado que se parte del diseño del MACH-I, la intención es lograr una longitud y sección más reducidas sin grandes pérdidas en maniobrabilidad.

La longitud está directamente relacionada con la sección y la carga soportada. Si consideramos un brazo robótico de sección reducida y longitud elevada, los esfuerzos que deberán soportar cada una de las articulaciones aumentarán considerablemente debido al propio peso del robot y la carga. De igual manera, si la sección se reduce en exceso, la tensión en los cables aumentará para poder compensar los esfuerzos provocados por la carga.

Como primera aproximación, se considera un diámetro máximo de 30 mm y una longitud de entre 25 y 35 cm.

3.2.2. Utillaje

Se espera que el brazo robótico sea capaz de realizar pequeñas inspecciones y/o manipulaciones. Para ello, se ha tenido en cuenta en los cálculos una capacidad de carga de 100 g equivalente a la sujeción de una cámara espía, unas pinzas, un imán, o cualquier otro posible acople en el extremo del robot.

### 3.3. Diseños conceptuales previos

Estudios previos realizados en el CAR sobre el desarrollo de manipuladores híper-redundantes [1], han identificado dos posibles opciones constructivas para el robot. A continuación, se van a presentar ambas, para después evaluar sus ventajas e inconvenientes y seleccionar así la más adecuada.

El primer diseño es un robot continuo basado en un endoscopio que utiliza articulaciones basadas en el modelo TPCJ. Por otro lado, el segundo prototipo se basa en un núcleo flexible o backbone donde no existen articulaciones localizadas.

DISEÑO MECÁNICO Y CONSTRUCCIÓN

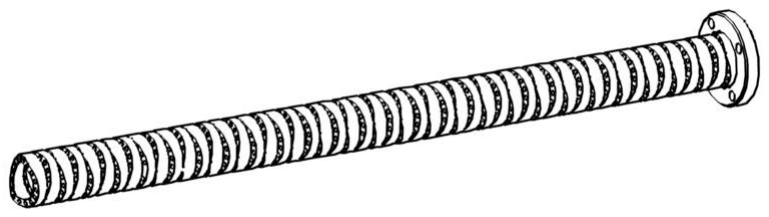
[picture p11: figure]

16 | ESCUELA TÉCNICA SUPERIOR DE INGENIEROS INDUSTRIALES (UPM)
3.3.1. Prototipo 1

El prototipo 1 es un brazo robótico de 17 mm de diámetro y 260 mm de longitud, y es el de construcción más compleja dado el diseño de direccionamiento de los cables.

Ilustración 22. Diseño CAD prototipo 1. Fuente: elaboración propia

Consta de cuatro secciones con una distribución de 20-12-12-8 discos desde la base hacia el extremo. Los discos siguen el modelo TPCJ y están desfasados 90º entre ellos de manera que los ejes de giro de cada sección quedan sin definir.

El accionamiento se realiza mediante
cables que quedan ocultos en el interior del propio
robot. En este diseño son necesarios cuatro
cables por sección debido al desfase mencionado en el párrafo anterior.

El número de secciones viene definido por el número de agujeros para cables que tiene cada disco, en este caso son 16. Si se desea que cada
sección únicamente pueda girar sobre un eje, es
decir, que no exista desfase entre discos, se
emplearían dos cables por sección únicamente y el número de secciones podría duplicarse, llegando a un máximo de ocho.
3.3.2. Prototipo 2

Este modelo tiene una sección de 30 mm y un núcleo flexible de sólo tres milímetros. Está compuesto por siete secciones con tres discos cada una de ellas para proporcionarle una mayor continuidad y, al igual que el prototipo anterior, es accionado mediante cables [1].

Ilustración 24. Diseño CAD prototipo 2. Fuente: [1]

Ilustración 23. Modelo TPCJ y desfase de 90º entre discos

CONSTRUCCIÓN Y CONTROL DE UN ROBOT CONTINUO DE CABLES CON DISCOS PIVOTANTES

ELENA MUÑOZ SÁNCHEZ | 17

Cada disco está formado por dos piezas idénticas atornilladas abrazando el núcleo flexible. En conjunto pueden albergar hasta 36 cables, por lo que, utilizando tres cables por sección, el brazo robótico podría ampliarse hasta un máximo de 12 secciones [1].

Ilustración 25. Disco prototipo 2 y eje flexible. Fuentes: [1] y https://amzn.to/2WA6ahA

El eje flexible posee una gran resistencia a torsión y compresión, pero no hay que olvidar la gran dependencia que supone para el modelo la elasticidad de la que esté dotado el eje.

3.3.3. Comparación de prototipos

A continuación, se exponen brevemente las principales características de ambos prototipos para así, justificar la decisión tomada.

Se trata de dos modelos de robot blando y continuo con un coste de fabricación realmente bajo. A su vez, ambos poseen una baja capacidad de carga, pero como su finalidad son pequeñas inspecciones, para la consideración de una carga máxima de 100 g es suficiente.

Sus diferencias se encuentran en las dimensiones, la facilidad de montaje y el tipo de eje. Pese a la facilidad de montaje del prototipo 2, la disposición de los discos del prototipo 1, su tamaño más reducido y su eje hueco proporcionan mayor libertad de movimiento y precisión. Además, la posibilidad de introducir por el interior el cableado del utillaje, supone una idea innovadora frente al resto de robots construidos con backbone.

### 3.4. Desarrollo

De aquí en adelante, se hará referencia al prototipo 1 como Pylori-I dado su diseño basado en un endoscopio y su gran parecido a la bacteria Helicobacter Pylori.

Ilustración 26. Bacteria Helicobacter Pylori y robot Pylori-I. Fuente: https://cinfasalud.cinfa.com/p/helicobacter-pylori/

DISEÑO MECÁNICO Y CONSTRUCCIÓN

18 | ESCUELA TÉCNICA SUPERIOR DE INGENIEROS INDUSTRIALES (UPM)

Como se ha comentado anteriormente en la comparación de los dos prototipos, este diseño consta de cuatro secciones actuadas por cuatro motores cada una de ellas, es decir, 16 motores en total.
Es posible añadir más secciones si los discos de cada sección se colocan sin desfase entre ellos, de manera que las secciones tengan un único eje de giro máximo.
Para este trabajo, se ha decidido continuar con la distribución planteada inicialmente: cuatro secciones con una distribución de discos de 20-12-12-8 partiendo desde la base. No se ha profundizado en el estudio de una distribución óptima de discos y secciones ya que esto era motivo de estudio de otro trabajo simultáneo [17].
A continuación, se reflejan las principales características del Pylori-I.

Tabla 1. Características del Pylori-I

Para comenzar con el desarrollo, es necesario analizar el caso más desfavorable de análisis de cargas. Estos cálculos servirán más adelante para determinar qué tipo de motor PaP va a emplearse.
La única carga a la que se somete el brazo robótico es su propio peso, aunque se le puede añadir una pequeña carga extra situada en el extremo para futuros utillajes que se puedan instalar. Hacer los cálculos con esta carga adicional nos asegura un margen de
Diámetro exterior del disco (mm) | Øe | 17
Diámetro interior del disco (mm) | Øi | 12
Diámetro de disposición de cables (mm) | Øc | 14.5
Diámetro agujero de cable (mm) | Øa | 0.9
Altura del disco (mm) | H | 4.8 ~ 5
Altura del pivote (mm) | h | 1.7
Desfase entre cables (º) | α | 22.5
Masa del disco (g) | mdisco | 0.49 ~ 0.5
Longitud total (mm) | L | 260
Longitud sección 1 (mm) | L1 | 100
Longitud sección 2 (mm) | L2 | 60
Longitud sección 3 (mm) | L3 | 60
Longitud sección 4 (mm) | L4 | 40
Número de secciones | M | 4
Número total de discos | N | 52
Discos en la sección 1 | N1 | 20
Discos en la sección 2 | N2 | 12
Discos en la sección 3 | N3 | 12
Discos en la sección 4 | N4 | 8
Cables por sección | n | 4
Ángulo máximo de giro del disco (rad) | βmax | 0.23
Ángulo máximo de giro de la sección 1 (rad) | Θ1 | 2.07
Ángulo máximo de giro de la sección 2 (rad) | Θ2 | 1.242
Ángulo máximo de giro de la sección 3 (rad) | Θ3 | 1.242
Ángulo máximo de giro de la sección 4 (rad) | Θ4 | 0.828

CONSTRUCCIÓN Y CONTROL DE UN ROBOT CONTINUO DE CABLES CON DISCOS PIVOTANTES

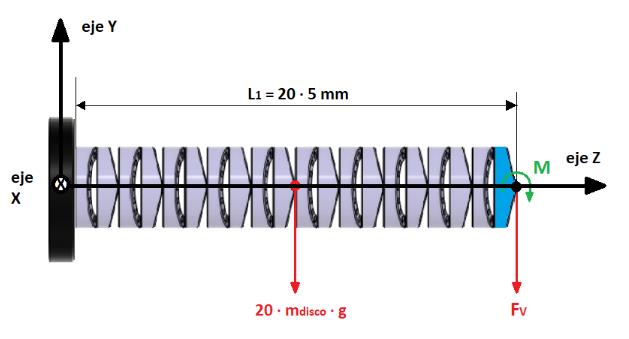
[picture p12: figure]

ELENA MUÑOZ SÁNCHEZ | 19

seguridad a la hora de instalar un utillaje o de manipular con unas pinzas objetos externos al robot que supongan un peso adicional en el extremo.
La carga del extremo se ha fijado en 100 g, que abarca la masa media de un utillaje (30 g los más pesados) más la de un objeto externo de hasta 80 g en algunos casos.
Se conoce el peso de cada disco, cinco gramos, y la altura máxima de los discos, 4.8 mm que se aproximan a cinco milímetros por las rugosidades de las piezas.
El caso más desfavorable se corresponde con la situación en la que el brazo robótico se encuentra en una posición completamente horizontal. En dicha posición el par generado es máximo, pues las masas de las secciones y del extremo se encuentran lo más alejadas posible de la base del brazo.

Ilustración 27. Diagrama de fuerzas en el brazo completo

Las longitudes de las secciones resultan L1 = 100 mm, L2 = 60 mm, L3 = 60 mm y L4 = 40 mm, lo cual implica una longitud total de 260 mm que entra dentro de los requisitos mencionados anteriormente. Sus masas son 10, 6, 6 y 4 gramos respectivamente. Sabiendo que mload = 100 g, suponemos una longitud media de 20 mm para simular el posible utillaje colocado en el extremo.
Partiendo de esta situación, la unión de las secciones 1 y 2 será la zona que soporte más par, por lo que se reduce el análisis a este punto:

Ilustración 28. Reducción de fuerzas

Fv y M son la fuerza y el par que los cables que generan el movimiento deberán compensar. Estos esfuerzos son calculados de la siguiente manera:

Fv = (6 + 6 + 4 + mload) ∙ g ∙ 10⁻3 = 1. 1368 N

DISEÑO MECÁNICO Y CONSTRUCCIÓN

20 | ESCUELA TÉCNICA SUPERIOR DE INGENIEROS INDUSTRIALES (UPM)

M = (6 + 6 + 4 + 1) ∙ 10⁻3

- mload ∙ g + (6 + 6 + 2) ∙ 10⁻3
- 4 ∙ 10⁻3
- g + (6 + 3)
- 10⁻3
- 6 ∙ 10⁻3
- g + 3 ∙ 10⁻3
- 6 ∙ 10⁻3
- g
= 0. 1666 + 0. 0055 + 0. 0053 + 0. 0018 = 0. 1792 N ∙ m

Los cables mencionados antes van a estar distribuidos equitativamente en los discos a lo largo de una circunferencia de 14.5 mm de diámetro y paralelamente al eje longitudinal del brazo robótico.
La distancia que hay desde los cables al eje de giro determina la tensión máxima que pueden soportar. El número de agujeros para cables de este prototipo es 16, que únicamente es múltiplo de cuatro, por tanto, para determinar esta fuerza máxima, se distinguen dos disposiciones de cuatro cables en una sección diferentes.

Ilustración 29. Distribución de cuatro cables y ejes de giro

Como se muestra en la figura anterior, para un mismo rcables, hay dos posibles ejes de giro. En el caso de giro respecto al eje 1 (o su perpendicular), actúan los cables 1 y 2 de manera opuesta (o los cables 3 y 4). En el caso de giro respecto al eje 2 o su perpendicular, los cables actúan por parejas, pudiéndose agrupar los cables 1 y 3 frente al 2 y 4, o los cables 1 y 4 frente al 2 y 3.

- Giro respecto al eje 1
En esta situación, el par generado por los cables 1 y 3 en el eje 1 es:

M1 = T ∙ rcables

- Giro respecto al eje 2
En esta otra situación, el par equivalente es generado únicamente por un cable: M2 = 2 · T · d2 = 2 · T · rcables · cos 45 = √2

2
- T · rcables

Como se puede observar, el caso más desfavorable es el giro en torno al eje 2, pues es la situación en la que se genera una tensión mayor.

CONSTRUCCIÓN Y CONTROL DE UN ROBOT CONTINUO DE CABLES CON DISCOS PIVOTANTES

ELENA MUÑOZ SÁNCHEZ | 21

### 3.5. Componentes, rediseño e impresión 3D

- Brazo robótico
El brazo robótico está formado por dos tipos de discos diferentes. Cada una de las secciones estará compuesta por Ni - 1 discos estándar con 16 agujeros pasantes y, como disco final, una modificación de éstos, que consiste en la adicción de 16 agujeros en la cara lateral para la posterior fijación del extremo de los cables.

Ilustración 30. Vista superior de un disco (válida para ambos tipos).

En los estudios previos realizados en CAR, tanto los discos estándar como los discos de final de sección tenían un diámetro (Øa) de 1.5 mm para las guías de los cables. Teniendo en cuenta que la diferencia entre el diámetro exterior y el interior es de cinco milímetros, los agujeros de los cables estaban rodeados por un margen de medio milímetro.

Este pequeño grosor corría el riesgo de romperse a causa de la fuerza que ejercen los cables en el final de sección o por el rozamiento que se genera dentro de las guías.

Como solución se rediseñaron las piezas con un Øa = 0.9 mm, siempre teniendo presente que reducir demasiado este diámetro puede causar complicaciones en la posterior construcción y aumentar en gran medida el rozamiento interior. Este diámetro proporciona el margen mínimo para poder pasar los cables sin dificultad durante la construcción.

Ilustración 31. Vista lateral de un disco estándar.

DISEÑO MECÁNICO Y CONSTRUCCIÓN

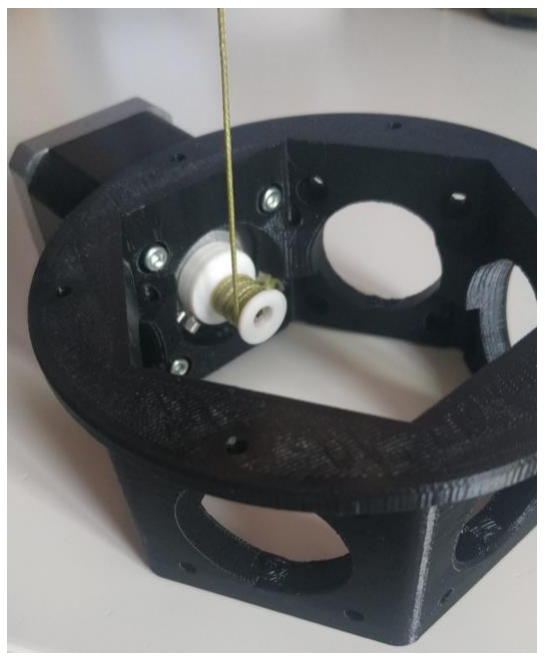
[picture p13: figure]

22 | ESCUELA TÉCNICA SUPERIOR DE INGENIEROS INDUSTRIALES (UPM)
- Distribuidor de cables
Esta pieza se ha diseñado para conseguir una distribución de los cables desde la base del brazo robótico lo más adaptada posible a la posición en la que se encuentran sus motores correspondientes.

Ilustración 32. Parte superior del distribuidor de cables

Tiene forma de embudo invertido y conduce los cables desde la parte superior por el interior de la pared de la pieza hasta la base, donde posteriormente se unirá con el banco de motores.

- Banco de motores
Está compuesto por tres piezas idénticas con forma de prisma hexagonal. Este diseño está pensado para que la distribución de motores se haga en tres pisos diferentes con la combinación deseada sin que influya la forma del banco de motores ni su posterior montaje.

Cada una de las bases hexagonales que componen el banco de motores tiene seis agujeros, uno en cada una de sus caras, para acoplar en ellos cada uno de los motores.

Ilustración 33. Montaje de un motor y su polea en una de las bases

CONSTRUCCIÓN Y CONTROL DE UN ROBOT CONTINUO DE CABLES CON DISCOS PIVOTANTES

ELENA MUÑOZ SÁNCHEZ | 23

En total hay 18 posibles acoplamientos de motores. Para este proyecto, únicamente se utilizarán 16 de los acoples, uno por cada cable, quedando dos libres que podrían emplearse en un futuro para el movimiento de una herramienta en el extremo del brazo robótico.

- Poleas
Las poleas han sido diseñadas en un tamaño los suficientemente reducido como para que permita su manipulación en el interior de las bases del banco de motores.

Están compuestos de un cilindro hueco dentro del cual se introduce el eje del motor PaP, un avellanado superior que dificulta que el cable enrollado alrededor del cilindro se salga, y una base más ancha en la que hay dos agujeros pasantes y un alojamiento para una tuerca.

Ilustración 34. Diferentes vistas de las poleas empleadas

De los dos agujeros pasantes, el más pequeño y vertical servirá para anudar el comienzo del cable que posteriormente se enrollará. Por otro lado, el grande se utilizará junto con la tuerca para alojar un tornillo que sirva como prisionero para sujetar el eje del motor.

- Soporte
Se ha diseñado en 3D un soporte sobre el que poder colocar el banco de actuadores sin interferir con los cables de los motores PaP. Se han añadido refuerzos para generar resistencia y que el material no se parta por el peso. De esta manera, se podrá tener el robot colocado en posición totalmente horizontal para trabajar con él.

Ilustración 35. Robot colocado sobre el soporte

DISEÑO MECÁNICO Y CONSTRUCCIÓN

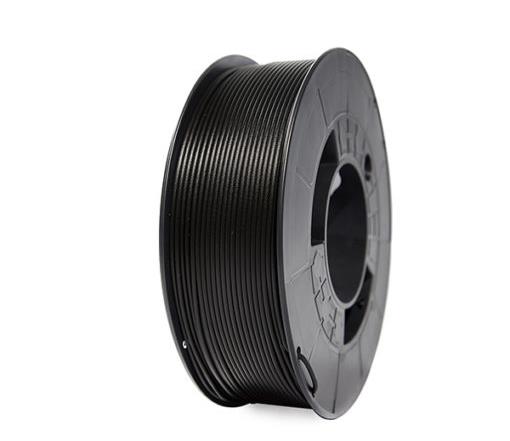
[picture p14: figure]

24 | ESCUELA TÉCNICA SUPERIOR DE INGENIEROS INDUSTRIALES (UPM)

### 3.6. Materiales

Debido a la precisión requerida en la impresión 3D de los discos que componen el robot, se ha optado por encargar a la empresa Proto Labs© la impresión de éstos. El tipo de material empleado para estas piezas es Nylon PA 12 blanco sinterizado por láser.

Ilustración 36. Bobina de Nylon PA12 Blanco. Fuente: https://www.3djake.es/fiberlogy/nylon-pa12-white

Por otro lado, el distribuidor de cables, las poleas, las bases del banco de actuadores y el soporte, han sido impresas por la Asociación de Estudiantes RESET utilizando como material PLA Negro. En el caso del soporte, se cambió a un color más llamativo para destacar que no forma parte del robot.

Ilustración 37. Bobina de PLA Negro. Fuente: https://www.impresoras3d.com/filamento/pla/

Para la actuación por cables se ha decidido emplear dos tipos diferentes de hilos de pescar para poder tener un punto de ensamblaje de los cables entre el banco de actuadores y el robot en caso de que sea necesario cambiar uno de los cables o acoplar un brazo robótico diferente.

Ilustración 38. Tipos de hilo empleados para la construcción. Fuente: https://www.amazon.es/

CONSTRUCCIÓN Y CONTROL DE UN ROBOT CONTINUO DE CABLES CON DISCOS PIVOTANTES

ELENA MUÑOZ SÁNCHEZ | 25

Dado que en la parte del banco de actuadores los cables sufrirán más por estar continuamente enrollándose y desenrollándose en las poleas, el cable empleado en esta fase será más grueso y resistente que el que recorrerá el brazo robótico.
Ambos cables se unirán entre ellos mediante una argolla metálica y nudos de pescar que funcionen bien cuando se aplica tensión en ellos.

Ilustración 39. Muestra del nudo empleado con los cables

Como protección ante posibles roturas de los cables por causas exteriores, se ha recubierto el brazo robótico con una malla elástica normalmente empleada como cubre cables. Se busca que aporte rigidez, pero sin oponer resistencia al movimiento natural del robot.

Ilustración 40. Malla cubre cables. Fuente: https://computacion.mercadolibre.com.ar/cables-hubs-usb/cables/mallas-cubre-cables/ (https://computacion.mercadolibre.com.ar/cables-hubs-usb/cables/mallas-cubre-cables/)

Finalmente, los motores elegidos como actuadores son unos motores PaP NEMA17 de 0.48 N.

Ilustración 41. Modelo de motor PaP utilizado en el proyecto

DISEÑO MECÁNICO Y CONSTRUCCIÓN

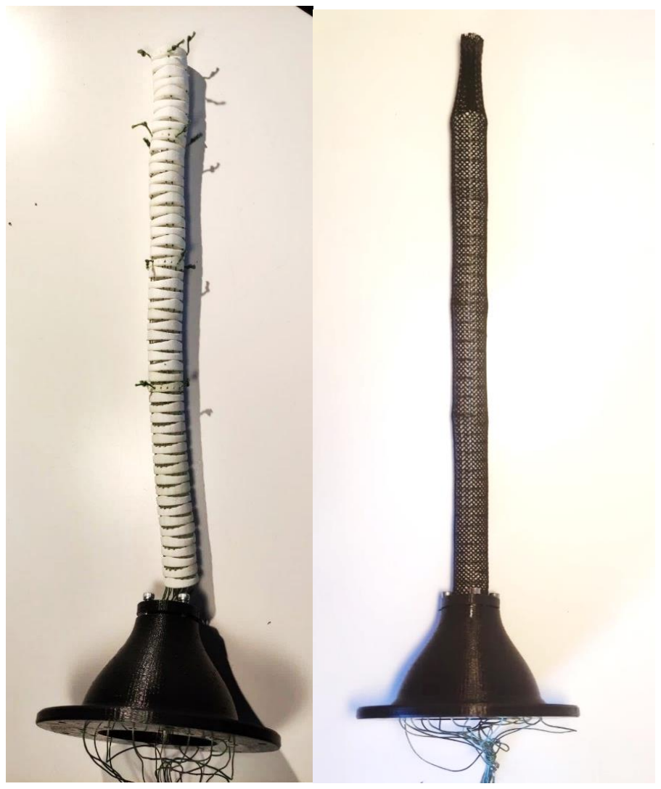
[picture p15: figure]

26 | ESCUELA TÉCNICA SUPERIOR DE INGENIEROS INDUSTRIALES (UPM)

Como se puede comprobar a continuación, partiendo de los cálculos realizados para el diseño, se dispone de un factor de seguridad de aproximadamente cuatro, lo cual permitiría en un futuro la incorporación de más discos en las secciones o el acople de una herramienta más pesada en el extremo del robot.

M1 = 0. 1792 N ∙ m = T ∙ rcables → T = 24. 72 N

Mmotor = T ∙ rpolea = 24. 72 ∙ 4. 5 ∙ 10⁻3 = 0. 11 N ∙ m

### 3.7. Construcción

A continuación, se va a resumir brevemente el paso a paso de la construcción del Pylori-I.
En primer lugar, con la ayuda de un “enhebrador”, se introducen uno a uno los cables por cada uno de los discos. Al llegar al final de la primera sección, cuatro de los cables deberán anudarse en el último disco, y habrá que tener en cuenta el desfase de la siguiente sección a la hora de empezar a introducir los cables por los discos de ésta.
Este proceso se realiza de igual manera en las sucesivas secciones, llegando únicamente cuatro cables al extremo final del robot.
El siguiente paso es guiar los cables desde la base del robot a través del distribuidor de cables y recubrir el brazo robótico con la malla elástica.

Ilustración 42. Brazo robótico antes y después de ser recubierto por la malla

CONSTRUCCIÓN Y CONTROL DE UN ROBOT CONTINUO DE CABLES CON DISCOS PIVOTANTES

ELENA MUÑOZ SÁNCHEZ | 27

Una vez sujeta la malla elástica en la base del brazo robótico, se procede con la unión entre los dos tipos de cable y entre el cable más grueso y las poleas de la manera que se ha descrito en el apartado de materiales.
Después, se instala la base de actuadores superior. Se extraen cinco de los cables con poleas por los agujeros para poder fijarlos a sus motores correspondientes y, finalmente, atornillar éstos a la base. Se procede de igual manera con las siguientes dos bases, extrayendo seis cables en la segunda, y cinco en la última.
La extracción de los cables mencionada se ha hecho siguiendo una distribución de motores que guarde una longitud de cable desde la polea hasta el nudo correspondiente lo más parecida posible para los 16 cables.

Ilustración 43. Resultado final del montaje.

De esta manera, en la base más cercana al brazo robótico, se encontrarán los cuatro motores pertenecientes a la última sección y uno de la tercera. En la base del medio, se atornillarán los motores restantes de la tercera sección junto a otros tres de la segunda. Y en la primera base, se hallarán los motores correspondientes a la primera sección junto con el cuarto de la segunda sección.
Finalmente, se coloca el robot horizontalmente sobre el soporte en la posición que sitúe el motor número uno en la parte superior del banco de actuadores, y se procede con la conexión al armario eléctrico.
Los cables empleados para estas conexiones se han fabricado de cero para poder asegurar un buen contacto en los conectores y evitar futuros fallos en el funcionamiento.

Ilustración 44. Cable y conectores para la conexión al armario

DISEÑO MECÁNICO Y CONSTRUCCIÓN

28 | ESCUELA TÉCNICA SUPERIOR DE INGENIEROS INDUSTRIALES (UPM)

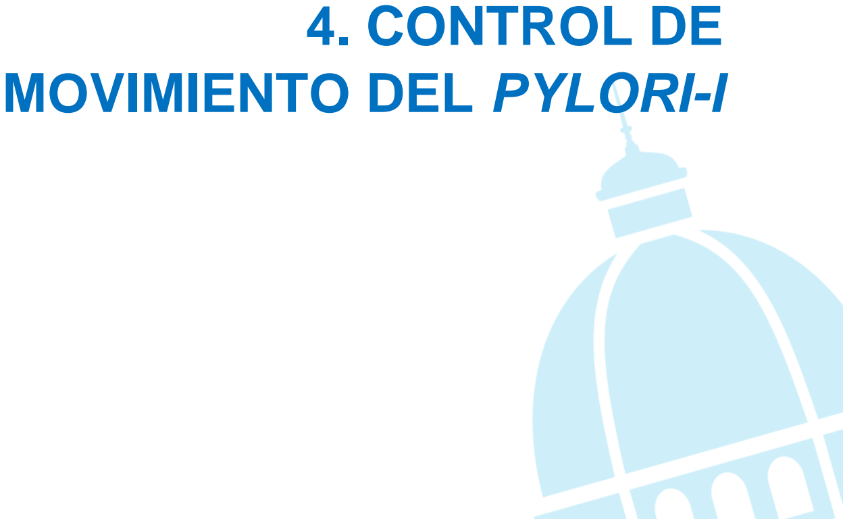
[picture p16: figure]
4. CONTROL DE MOVIMIENTO DEL PYLORI-I

CONSTRUCCIÓN Y CONTROL DE UN ROBOT CONTINUO DE CABLES CON DISCOS PIVOTANTES

ELENA MUÑOZ SÁNCHEZ | 29

### 4. CONTROL DE MOVIMIENTO DEL PYLORI-I

### 4.1. Estudio de las cinemáticas

Para el control de movimiento del Pylori-I se ha utilizado como base el entorno y las cinemáticas del Trabajo de Fin de Grado de Jaime Bravo [17] que se han desarrollado con el programa Matlab.
Dado que, en dicho trabajo, el robot con el que se trabaja en simulación tiene un comportamiento ideal, es decir, sin restricciones ni detección de colisiones, se debe realizar un estudio de las diferentes cinemáticas implementadas para decidir cuál serviría para un comportamiento real del Pylori-I.
Tras la implementación del ángulo máximo de giro de cada disco respecto al anterior (βmax=0.23 rad) como restricción en cada una de las cinemáticas, se ha observado que dos de las tres cinemáticas disponibles dejan de comportarse de manera adecuada.
Como ejemplo, se ha decidido posicionar el extremo del robot en la posición [-150 -100 180] para visualizar por qué se descartan las dos cinemáticas que emplean el Método de la Jacobiana.

Ilustración 45. A la izquierda, Método de la Jacobiana utilizando como variables los ángulos de los discos. A la derecha, Método de la Jacobiana utilizando como variables los ángulos de las secciones

Aunque a primera vista parezca que la cinemática que emplea los ángulos de las secciones del robot como parámetros para el cálculo de la matriz Jacobiana posiciona el extremo del robot correctamente, si se observa la posición real del extremo junto con el error de posicionamiento existente, se puede concluir que dista mucho de encontrarse en la pose deseada.
Por otro lado, para ese mismo punto, el control cinemático mediante el Descenso del Gradiente genera un error 20 veces más pequeños que en los casos anteriores. De esta manera, se termina que la cinemática que se va a utilizar para el control de movimiento del Pylori-I será ésta última.

Ilustración 46. Posición real del extremo y error generado con el Método del Descenso del Gradiente.

CONTROL DE MOVIMIENTO DEL PYLORI-I

30 | ESCUELA TÉCNICA SUPERIOR DE INGENIEROS INDUSTRIALES (UPM)

Ilustración 47. Posicionamiento del extremo mediante el Método del Descenso del Gradiente.

### 4.2. Posicionamiento del extremo

Una vez decidido el control cinemático que se va a utilizar, la llamada a la función empleada para el posicionamiento del extremo queda de la siguiente manera:

[newConfig, error, iter] = move(robot, X, Y, Z, 'GradientDescent');

Los datos ‘X’, ‘Y’, ’Z’ que se introducen en la llamada son las coordenadas del punto en el que se desea situar el extremo. Como se verá a continuación, en el caso de las trayectorias, serán vectores de datos.

### 4.3. Generación de trayectorias

La generación de trayectorias dota al robot de una mayor precisión a la hora de posicionar el extremo y de una mayor maniobrabilidad si se necesita evitar obstáculos.
La función encargada de generar los vectores de coordenadas para cada uno de los puntos que componen la trayectoria es la siguiente:

[X, Y, Z] = trayec(type, N, start, goal)

En el commando ‘type’ se puede introducir dos tipos diferentes de trayectoria. Por un lado, se encuentra el tipo ‘HELICE’, el cual únicamente genera una trayectoria helicoidal determinada para comprobar la flexibilidad del movimiento del robot siguiendo estas ecuaciones:

case 'HELICE'
n=12/N;
t=8:n:20;

X = 130*sin(t);
Y = 130*cos(t);

CONSTRUCCIÓN Y CONTROL DE UN ROBOT CONTINUO DE CABLES CON DISCOS PIVOTANTES

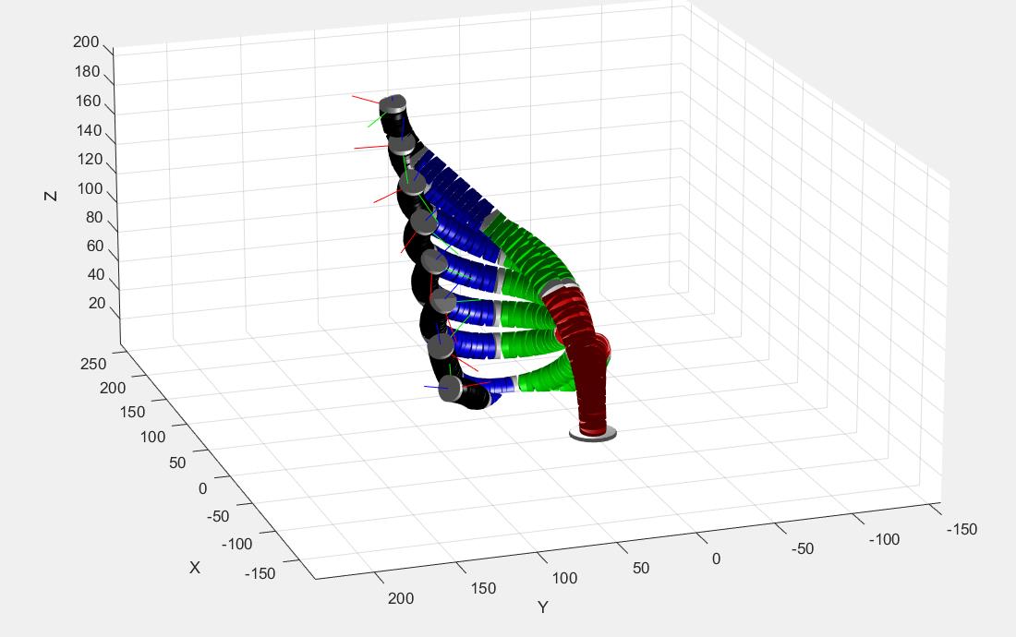
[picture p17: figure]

ELENA MUÑOZ SÁNCHEZ | 31

Z=10*t;

Por otro lado, se encuentra el tipo ‘RECT’ encargado de generar una trayectoria rectilínea entre dos puntos dados.

Ilustración 48. Ejemplo de generación de trayectoria rectilínea

El dato ‘N’ recoge el número de puntos menos uno en los que se quiere dividir la trayectoria. Por último, los datos ‘start’ y ‘goal’ sólo se utilizan en el caso de la trayectoria rectilínea. Representan el vector de coordenadas iniciales y finales de la trayectoria respectivamente.

### 4.4. Detección de colisiones

La detección de colisiones, en lugar de implementarla como una función, se ha decidido añadirla dentro de los atributos y métodos públicos de la clase ‘HRRTree’.
Este método compara la posición relativa entre los discos dos a dos, exceptuando los discos contiguos, y detecta si hay colisión entre ellos mediante la creación de mallas a partir del archivo .stl de los discos que conforman el robot.
El código del método implementado se muestra a continuación:

%% COLISIONES
function [n,colision] = colisiones (obj, newConfig)
stl = stlread('Mod_Boro_Triang.stl');

disco1 = collisionMesh(stl.Points);
disco2 = collisionMesh(stl.Points);

colision = {};
n=0;

for j=1:obj.TotalLinks-2
for i=j:obj.TotalLinks-2
disco1.Pose = getTransform (obj, newConfig, obj.BodyNames{1,j}); disco2.Pose = getTransform (obj, newConfig, obj.BodyNames{1,i+2});

if checkCollision(disco1,disco2)==1

CONTROL DE MOVIMIENTO DEL PYLORI-I

32 | ESCUELA TÉCNICA SUPERIOR DE INGENIEROS INDUSTRIALES (UPM)

n=n+1;
colision (n,:) ={obj.BodyNames{1,j},obj.BodyNames{1,i+2}}; end
end
end
end

### 4.5. Cálculo de longitudes

Para el cálculo de las longitudes de los cables necesarias para el posicionamiento del Pylori-I, hay que tener en cuenta que la elongación de los cables de cada sección depende de la correspondiente a las secciones anteriores.
Por tanto, se debe calcular la longitud de cada cable a su paso por cada sección y sumar cada uno de los resultados para hallar la longitud final. Conociendo la longitud en reposo de cada uno de los cables, se podrá hallar sin dificultad la elongación de cada uno (∆Li).
A continuación, se muestra el procedimiento para el cálculo de la longitud de un cable a lo largo de una sección, siendo análogo para el resto de los cables y secciones.

Ilustración 49. Representación de los ángulos θ, φ y α de la sección. Fuente: Modificado de [17]

El giro de una sección genera una curvatura en su eje central de radio R y cuyo ángulo formado con el plano horizontal se denomina α. De igual manera, se genera una curvatura con el mismo ángulo por cada uno de los ejes guía de los cables, cuyos radios llamaremos Rgi.
Siendo γ los ángulos α representados en la Ilustración 50, los cuales simbolizan el ángulo entre el radio de curvatura R y la posición del cable del que se quiere calcular la longitud, y conocidos rcables, θ y φ (los dos últimos los proporciona un método de los implementados en la clase ‘HRRTree’ en Matlab [17]), se procede con el cálculo de Rg.

β = γ − φ − π
Rg = R + rcables ∙ cos β

L = R ∙ α

CONSTRUCCIÓN Y CONTROL DE UN ROBOT CONTINUO DE CABLES CON DISCOS PIVOTANTES

ELENA MUÑOZ SÁNCHEZ | 33

θ = α
Lg = Rg ∙ θ = L + rcables ∙ θ ∙ cosβ

Ilustración 50. Proyección de los vectores rotación de las articulaciones. Fuente: [17]

### 4.6. Transformación de longitud a pulsos

Una vez calculada la elongación de cada uno de los cables, se llama a la siguiente función proporcionándole un vector que alberga cada una de las elongaciones calculadas.

function [pulsos,vel] = long2pulsos(hilos) % 1600 pulsos/rev
% 28,27 mm/rev
% ~~57 pulsos/mm
% Movimiento en un máximo de 3 sec

for i=1:16
pulsos(i)= 57*hilos(i);
vel(i)=abs(pulsos(i))/3;
end
end

Mediante proporcionalidad, se puede calcular a partir del ángulo máximo de giro de un disco, los milímetros que el hilo se acorta o alarga por cada revolución del eje del motor correspondiente. En este caso, 28.27 mm/rev. Dado que los motores están configurados para tener 1600 pulsos por revolución, se llega a la conclusión de que, por cada milímetro de elongación, el motor gira aproximadamente 57 pulsos.

### 4.7. Espacio de trabajo

Inicialmente, se implementó una función en Matlab que calculaba el espacio de trabajo para cualquiera de las cinemáticas de control. A continuación, se mostrarán ejemplos hechos únicamente utilizando la cinemática del Descenso del Gradiente que es la que se ha considerado válida.
En primer lugar, se ha calculado un primer caso en el que se evalúan 1331 puntos dentro de los límites establecidos para el entorno de trabajo, y realizando un máximo de 250 iteraciones como máximo en el cálculo del posicionamiento.

CONTROL DE MOVIMIENTO DEL PYLORI-I

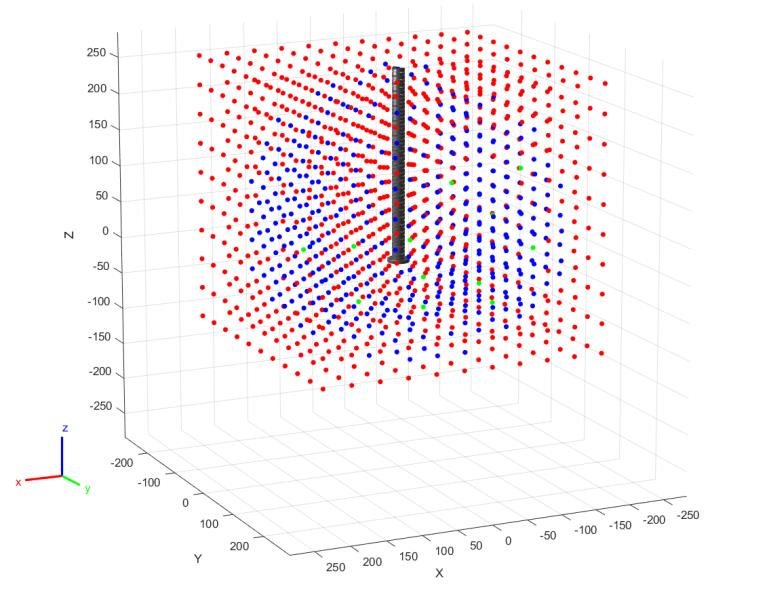
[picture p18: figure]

34 | ESCUELA TÉCNICA SUPERIOR DE INGENIEROS INDUSTRIALES (UPM)

En color azul, se representan los puntos a los que el robot es capaz de llegar con un error de entre tres y diez milímetros. De color verde, se encuentran los puntos con un error de posicionamiento inferior a tres milímetros y, en rojo, aquello puntos cuyo error sea superior a 10 mm.

Ilustración 51. Espacio de trabajo evaluado para 1331 puntos y 250 iteraciones

Como se puede observar, apenas se obtienen puntos con errores inferiores a tres milímetros, por lo que se aumenta el número de puntos evaluados a 2520, lo cual significa barrer el entorno de cuatro en cuatro centímetros.

Ilustración 52. Espacio de trabajo evaluado para 2520 puntos y 250 iteraciones

El resultado del análisis mejora significativamente. Teniendo en cuenta que el robot nunca va a ser capaz de acceder a los vértices del espacio que conforma su entorno de trabajo, la densidad de puntos verdes y azules respecto a los rojos se considera adecuada para seguir adelante.

Ilustración 53. Densidad en porcentaje de cada tipo de punto respecto al total

CONSTRUCCIÓN Y CONTROL DE UN ROBOT CONTINUO DE CABLES CON DISCOS PIVOTANTES

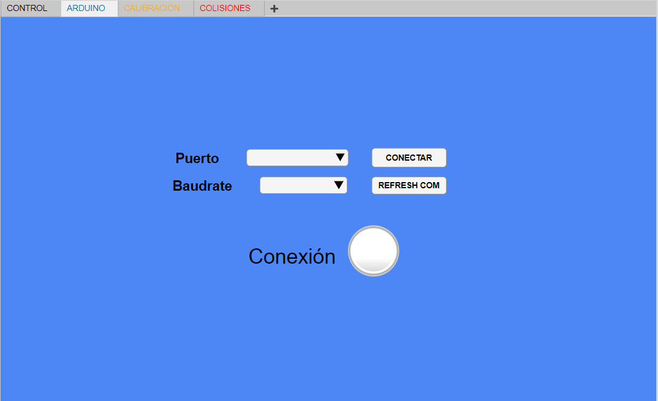
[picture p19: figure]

ELENA MUÑOZ SÁNCHEZ | 35

### 4.8. Interfaz hombre-máquina

La pantalla principal de la interfaz hombre-máquina (IHM) es la mostrada a continuación.

Ilustración 54. Pantalla principal de control de la IHM

En esta pantalla se introducen las coordenadas de posicionamiento y se selecciona el tipo de control cinemático deseado. Cuando se pulsa en el botón ‘SIMULAR’, la IHM genera una simulación que muestra el posicionamiento del robot en 3D, muestra en pantalla la posición real en la que se encuentra el TCP, y el error de posicionamiento existente. Además, si el error es demasiado grande o se genera una colisión, el piloto ‘Punto válido’ cambiará a color rojo.
En la segunda pestaña, se encuentra la pantalla utilizada para la conexión Matlab-Arduino. Una vez seleccionado el puerto COM y el baudrate, se pulsa en ‘CONECTAR’ y si el procedimiento se ha realizado de manera correcta, el piloto ‘CONEXIÓN’ cambiará a color verde y en el botón ‘CONECTAR’ pasará a poner ‘DESCONECTAR’.

Ilustración 55. Pantalla de conexión Matlab-Arduino de la IHM

La tercera pestaña se ha creado para automatizar el proceso de calibración, pudiendo seleccionar el motor que se desee calibrar e introducir el número de pulsos que debe girar el motor. Una vez terminado el proceso con todos los motores, se pulsa el botón ‘FIJAR HOME’ para que los motores consideren esa posición actual como HOME o posición de reposo.

CONTROL DE MOVIMIENTO DEL PYLORI-I

36 | ESCUELA TÉCNICA SUPERIOR DE INGENIEROS INDUSTRIALES (UPM)

Ilustración 56. Pantalla de calibración de la IHM

Finalmente, en la cuarta pestaña, se muestra una tabla en la que aparecerán los discos implicados en las colisiones generadas tras la simulación del posicionamiento deseado, así como el número total de colisiones que se hayan producido.

Ilustración 57. Pantalla de colisiones y ejemplo

# 5. HARDWARE DE CONTROL

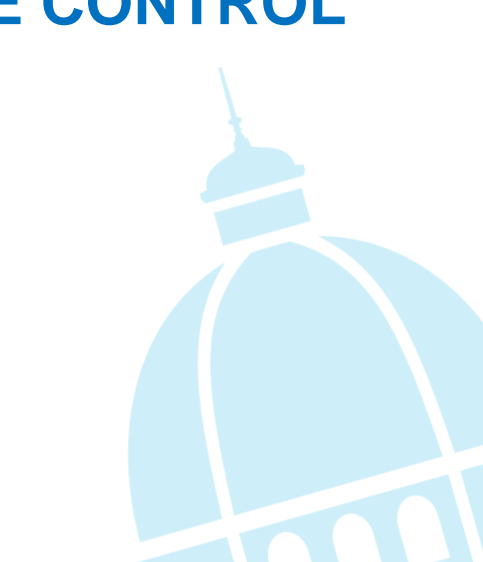
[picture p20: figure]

CONSTRUCCIÓN Y CONTROL DE UN ROBOT CONTINUO DE CABLES CON DISCOS PIVOTANTES

ELENA MUÑOZ SÁNCHEZ | 37

### 5. HARDWARE DE CONTROL

### 5.1. Armario eléctrico

La utilización de este armario eléctrico se basa en el objetivo de controlar los 16 motores paso a paso que actúan en este robot.
El armario permite controlar hasta un total de 18 motores PaP con una corriente máxima de 3.5 A por motor.

Ilustración 58. Armario eléctrico para 18 motores PaP

Los dispositivos de control instalados en su interior son drivers TB6600, los cuales son controlados mediante un Arduino Due que recibe los comandos de control mediante Serial. Los switches laterales de los TB6600 dan la posibilidad de configurar la corriente y los micropasos con los que se controlarán los diferentes motores PaP. Dichos parámetros, quedan establecidos según las siguientes tablas:

Tabla 2. Configuración de los micropasos para un motor de 200 pasos

Micro Step | Pulse/rev | S1 | S2 | S3
NC | NC | ON | ON | ON
1 | 200 | ON | ON | OFF
2/A | 400 | ON | OFF | ON
2/B | 400 | OFF | ON | ON
4 | 800 | ON | OFF | OFF
8 | 1600 | OFF | ON | OFF
16 | 3200 | OFF | OFF | ON
32 | 6400 | OFF | OFF | OFF

HARDWARE DE CONTROL

38 | ESCUELA TÉCNICA SUPERIOR DE INGENIEROS INDUSTRIALES (UPM)

Tabla 3. Configuración de los de la corriente para un motor de 200 pasos

Current (A) | PK Current (A) | S4 | S5 | S6
0.5 | 0.7 | ON | ON | ON
1 | 1.2 | ON | OFF | ON
1.5 | 1.7 | ON | ON | OFF
2.0 | 2.2 | ON | OFF | OFF
2.5 | 2.7 | OFF | ON | ON
2.8 | 2.9 | OFF | OFF | OFF
3.0 | 3.2 | OFF | ON | OFF
3.5 | 4.0 | OFF | OFF | OFF

Ilustración 59. Interior del armario eléctrico y distribución de drivers

La configuración elegida para los motores del Pylori-I es OFF-ON-OFF-ON-OFF-OFF (S1-S2-S3-S4-S5-S6), es decir, un microstep de 8 y una corriente de 2 A. Dado que los motores son de 200 pasos, tras realizar el microstepping, pasarán a tener 1600 pulsos/revolución.
Los motores PaP se conectan al armario mediante conectores de cuatro pines de la siguiente manera:

Ilustración 60. Conexión de los motores PaP al armario

CONSTRUCCIÓN Y CONTROL DE UN ROBOT CONTINUO DE CABLES CON DISCOS PIVOTANTES

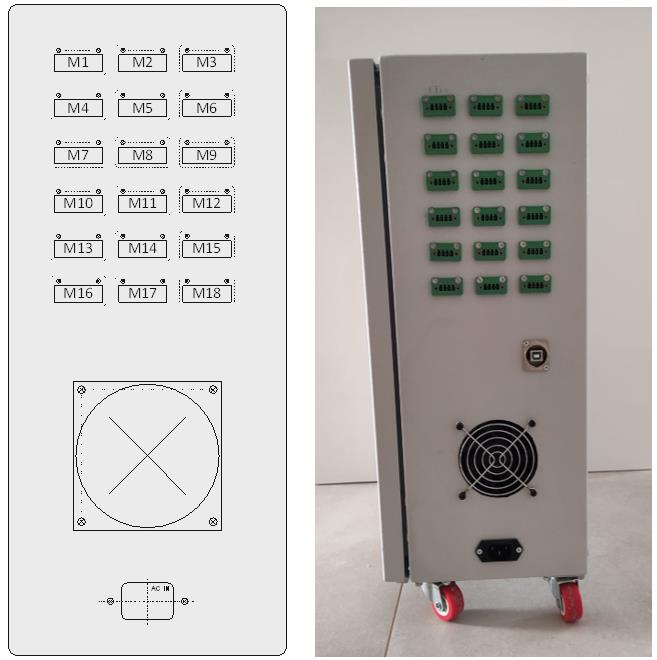
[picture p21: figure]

ELENA MUÑOZ SÁNCHEZ | 39

La numeración de los 18 conectores en la cara lateral derecha es la que se muestra en la siguiente ilustración:

Ilustración 61. Distribución de los conectores

5.1.1. Puesta en marcha del armario

El primer paso es conectar los 16 motores y enchufar el armario eléctrico a la corriente. Una vez conectados todos los cables correctamente, se procede con la puesta en marcha.

El armario cuenta con diferentes protecciones que se deben tener en cuenta a la hora de ponerlo en marcha. En primer lugar, será necesario abrir el armario y cerciorarse de que el interruptor magnetotérmico situado en su interior esta activado. Una vez realizada esta comprobación, es recomendable cerrar el armario.

El siguiente paso será comprobar que la seta de emergencia no está pulsada. En caso de estarlo, la seta de emergencia se libera girándola sobre sí misma.

Por último, se colocará el interruptor de encendido en posición ON. Automáticamente, el armario arrancará y los ventiladores comenzarán a funcionar. A partir de aquí, será posible enviar los comandos mediante Serial.

5.1.2. Tabla de equivalencia

La tabla mostrada a continuación relaciona los pines del Arduino Due con los drivers TB6600:

HARDWARE DE CONTROL

40 | ESCUELA TÉCNICA SUPERIOR DE INGENIEROS INDUSTRIALES (UPM)

Tabla 4. Correspondencia entre pines de Arduino y señales de los drivers

Arduino
PIN
| Función | Motor
13 | PUL+ | 1
12 | DIR+ | 1
11 | PUL+ | 2
10 | DIR+ | 2
9 | PUL+ | 3
8 | DIR+ | 3
7 | PUL+ | 4
6 | DIR+ | 4
5 | PUL+ | 5
4 | DIR+ | 5
3 | PUL+ | 6
2 | DIR+ | 6
14 | PUL+ | 7
15 | DIR+ | 7
16 | PUL+ | 8
17 | DIR+ | 8
18 | PUL+ | 9
19 | DIR+ | 9
20 | PUL+ | 10
21 | DIR+ | 10
22 | PUL+ | 11
23 | DIR+ | 11
24 | PUL+ | 12
25 | DIR+ | 12
26 | PUL+ | 13
27 | DIR+ | 13
28 | PUL+ | 14
29 | DIR+ | 14
30 | PUL+ | 15
31 | DIR+ | 15
32 | PUL+ | 16
33 | DIR+ | 16
34 | PUL+ | 17
35 | DIR+ | 17
36 | PUL+ | 18
37 | DIR+ | 18
48 | ENA | 1;2;3
49 | ENA | 4;5;6
50 | ENA | 7;8;9
51 | ENA | 10;11;12
52 | ENA | 13;14;15
53 | ENA | 16;17;18

CONSTRUCCIÓN Y CONTROL DE UN ROBOT CONTINUO DE CABLES CON DISCOS PIVOTANTES

ELENA MUÑOZ SÁNCHEZ | 41

### 5.2. Arduino

El control de los motores se realiza enviando comandos mediante el Serial de Arduino. Para iniciar el movimiento es necesario establecer la comunicación con los siguientes parámetros:

Parámetro | Valor
Baudrate | 250000
DataBits | 8
StopBits | 1
Parity | None

Una vez iniciado el puerto Serial, el control se realizará siguiendo una sintaxis básica para el envío de mensajes, la cual tiene la siguiente forma:
[Motor;Comando;Arg1;Arg2;]

Como se puede observar, el inicio y el final del mensaje están marcados por el carácter “[“ y “]” respectivamente, y después del último dato hay también un “;”.
El parámetro Motor selecciona el motor al cual va dirigido el comando, por lo que podrá tomar valores desde 1 a 18.
El parámetro Comando puede tomar 4 valores, los cuales determinan la acción que se llevará a cabo. Dependiendo del comando, serán necesarios los argumentos o no. Todo ello se recoge en la siguiente tabla.

Tabla 5. Descripción de los comandos disponibles

Comando | Acción | Arg1 | Arg2 | Descripción
0 | Disable | | | Deshabilita el motor correspondiente*

1

Speed
Mode**

Velocidad
(Steps/s)

Modo velocidad que establece los pulsos por segundo a los que se moverá el motor. Un valor negativo invierte el sentido de giro.

No se recomiendan velocidades superiores a 4000 steps/s

2

Servo
Mode

Velocidad
(Steps/s)

Posición
(Pulsos)

Modo servo donde se fija una posición objetivo y se condiciona la velocidad del recorrido

3

Set
Position Posición

Establece la posición actual al valor que se le indica. La posición al inicio del programa es 0

*Los motores se deshabilitan por grupos de 3, por lo que no es posible deshabilitar independientemente cada motor. Para consultar que motores se activan y desactivan con la misma señal, consultar la tabla de correspondencia al final del documento.

**Pese a estar en modo velocidad, los pulsos desplazados son contabilizados, por lo que si posteriormente se utiliza el modo servo habrá que tener esto en cuenta.

OPERACIÓN

42 | ESCUELA TÉCNICA SUPERIOR DE INGENIEROS INDUSTRIALES (UPM)
5.2.1. Ejemplo
[2;1;2000;] | //Motor 2 se comienza a mover a 2000 pulsos/s
[2;1;-1000;] | //Motor 2 invierte su sentido de giro y se mueve a 1000
pulsos/s
[2;1;0;] | //Se detiene el motor 2
[2;3;1500;] | //Se establece la posición actual del motor 2 a 1500
pulsos.

[2;2;2000,8000;] //Se mueve hasta la posición 8000 (desde la 1500) a 2000 pulsos/s.

[2;0;] | //Se deshabilita motor 2, deja de llegar corriente al motor

### 5.3. Relación longitud-pulsos

Para transformar la longitud de acortamiento o alargamiento que nos proporciona Matlab de cada uno de los cables, hay que tener en cuenta las dimensiones de las poleas descritas anteriormente en el diseño.
Estas poleas tienen un diámetro de 9 mm en el eje central, por lo que la longitud recogida por cada vuelta dada en la polea es
| 2π ∙ 4. 5 = 28. 2743 mm
Sabiendo que a cada motor le corresponden 1600 pulsos por revolución según el ajuste de microstepping explicado recientemente, y utilizando proporcionalidad, obtenemos que 1 mm recogido corresponde a 56.588 pulsos, los cuales se han redondeado a 57 en el código.

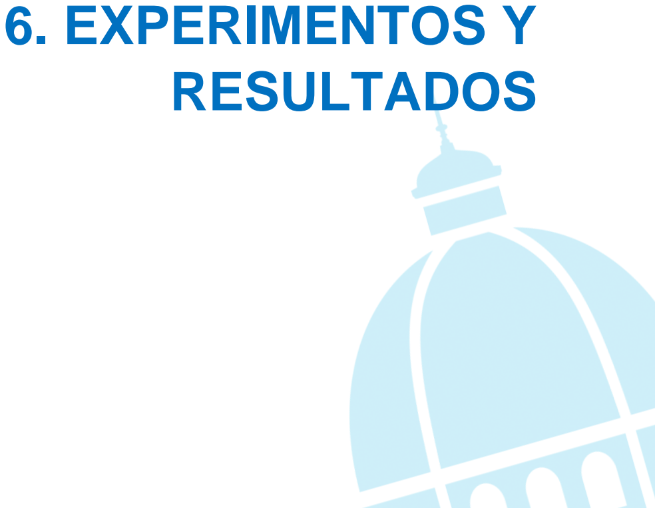
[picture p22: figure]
6. EXPERIMENTOS Y RESULTADOS

CONSTRUCCIÓN Y CONTROL DE UN ROBOT CONTINUO DE CABLES CON DISCOS PIVOTANTES

ELENA MUÑOZ SÁNCHEZ | 43

### 6. EXPERIMENTOS Y RESULTADOS

### 6.1. Espacio de trabajo

El espacio de trabajo físico ha sido construido mediante perfiles de aluminio, piezas diseñadas en 3D, carros V-Slot y láseres. Las dimensiones han seguido el resultado obtenido en el cálculo del espacio de trabajo con Matlab, permitiendo al robot moverse vertical y horizontalmente a lo largo de 400 mm.

Ilustración 62. Visión general del espacio de trabajo y posicionamiento del Pylori-I en el mismo

En los perfiles que componen el espacio de trabajo se han instalado cuatro láseres. Dos de ellos, son láseres lineales y se encuentran fijos en la estructura. Son aquellos que se utilizarán para corroborar que la calibración es correcta.

Ilustración 63. Láseres lineales

Por otro lado, los dos restantes, son láseres de punto que se desplazarán con la ayuda de los carros V-Slot hasta apuntar al TCP. En ese instante, teniendo claro el origen de coordenadas y los ejes de referencia del espacio de trabajo, se procede con la obtención de las coordenadas X, Y, Z de la posición en la que se encuentra el extremo del robot.

EXPERIMENTOS Y RESULTADOS

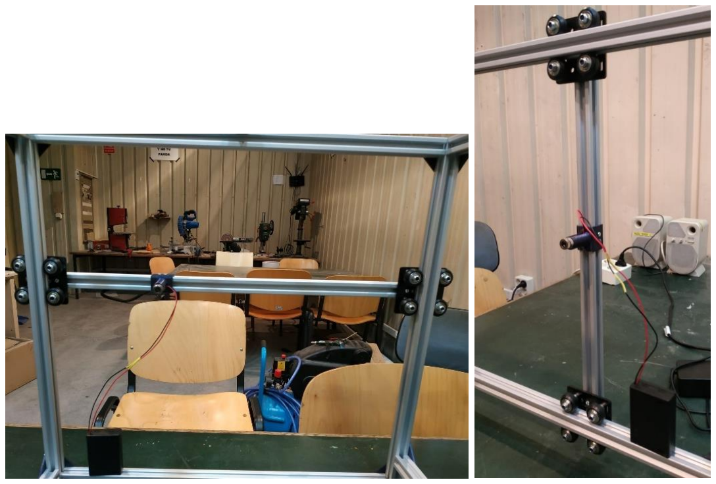
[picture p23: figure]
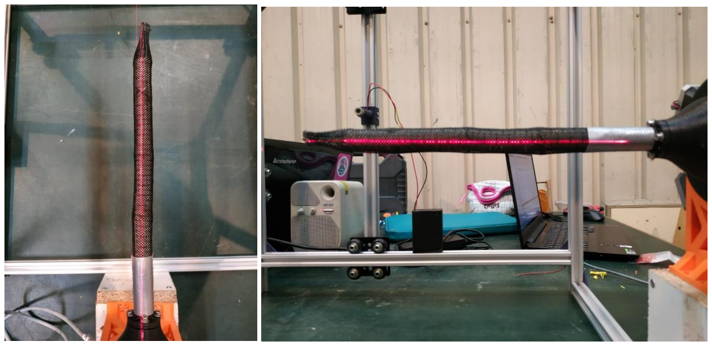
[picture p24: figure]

44 | ESCUELA TÉCNICA SUPERIOR DE INGENIEROS INDUSTRIALES (UPM)

Ilustración 64. Láseres de punto y carros V-Slot

### 6.2. Puesta en marcha

La puesta en marcha del robot consiste, básicamente, en la calibración de éste. Para llevar a cabo este proceso, se ha diseñado en Matlab la siguiente función:

function calibrarArduino(Arduino,modo,motor,pul);

Los modos implementados dentro de esta función son cuatro. El modo ‘0’ establece la posición actual de todos los motores como el HOME (recomendable realizar este paso antes de comenzar a calibrar).
El modo ‘1’ permite mandar a Arduino un número de pasos a un motor concreto. De esta manera se tensará cada uno de los cables hasta conseguir una posición de reposo alineada con los láseres como se muestra a continuación.

Ilustración 65. Pylori-I completamente alineado tras la calibración

CONSTRUCCIÓN Y CONTROL DE UN ROBOT CONTINUO DE CABLES CON DISCOS PIVOTANTES

ELENA MUÑOZ SÁNCHEZ | 45

El modo ‘2’ funciona de igual manera que el primero de todos, a excepción de que permite seleccionar de qué motor quieres fijar la posición como HOME.
Finalmente, el modo ‘3’ es el ‘RESET’. Envía la posición HOME a todos los motores quedando el robot en la pose de reposo inicial.

### 6.3. Realización de pruebas

A continuación, se muestran tres tablas diferentes con parte de los experimentos realizados. Se estudian los mismos vectores de coordenadas para diferentes casos.

Tabla 6. Pruebas de posicionamiento del extremo

Posición del extremo deseada (mm) | Posición real (mm)
X | Y | Z | X | Y | Z | Error (mm)
104 | 104 | 200 | 65 | 50 | 215 | 68,28
-100 | 100 | 170 | -90 | 70 | 200 | 43,59
120 | -150 | 200 | 85 | -80 | 190 | 78,90
-70 | -70 | 150 | -90 | -60 | 190 | 45,83
-150 | -100 | 180 | -75 | -55 | 200 | 89,72

Tabla 7. Pruebas de posicionamiento mediante trayectoria rectilínea (N = 6)

Posición final deseada de la trayectoria (mm)

Posición final real de la
trayectoria (mm)
X | Y | Z | X | Y | Z | Puntos | Error (mm)
104 | 104 | 200 | 65 | 60 | 220 | 6 | 62,10
-100 | 100 | 170 | -110 | 75 | 180 | 6 | 28,72
120 | -150 | 200 | 90 | -105 | 190 | 6 | 55,00
-70 | -70 | 150 | -100 | -40 | 145 | 6 | 42,72
-150 | -100 | 180 | -90 | -120 | 190 | 6 | 64,03

Tabla 8. Pruebas de posicionamiento mediante trayectoria rectilínea (N = 12)

Posición final deseada de la trayectoria (mm)

Posición final real de la
trayectoria (mm)
X | Y | Z | X | Y | Z | Puntos | Error (mm)
104 | 104 | 200 | 70 | 85 | 180 | 12 | 43,78
-100 | 100 | 170 | -100 | 60 | 190 | 12 | 44,72
120 | -150 | 200 | 95 | -80 | 200 | 12 | 74,33
-70 | -70 | 150 | -85 | -90 | 170 | 12 | 32,02
-150 | -100 | 180 | -75 | -85 | 190 | 12 | 77,14

EXPERIMENTOS Y RESULTADOS

46 | ESCUELA TÉCNICA SUPERIOR DE INGENIEROS INDUSTRIALES (UPM)

### 6.4. Discusión de los resultados

A la vista de los resultados obtenidos, se llega a la conclusión de que el comportamiento físico del Pylori-I no es el esperado, ya que el error de posicionamiento es muy superior al obtenido en simulación.
Esta gran diferencia puede estar provocada por la dificultad de corroborar que la tensión de los cables es la adecuada, puesto que no se tiene acceso a ellos. También es posible que la causa sea la distensión progresiva de los cables según avanza el proceso de experimentación, o el propio rozamiento que se genera en las guías de los cables.
Por otro lado, si se observan los datos con detenimiento, se pueden sacar cosas en claro. Por ejemplo, el error de posicionamiento del extremo por lo general es menor si el movimiento se realiza siguiendo una trayectoria rectilínea en lugar de un movimiento directo. Sin embargo, entre realizar las trayectorias con el doble de puntos intermedios o no, no se aprecian grandes diferencias y el error es mayor en un caso o en otro independientemente de este número. Por tanto, se deduce que este número N no es determinante para estos casos.

# 7. LÍNEAS FUTURAS

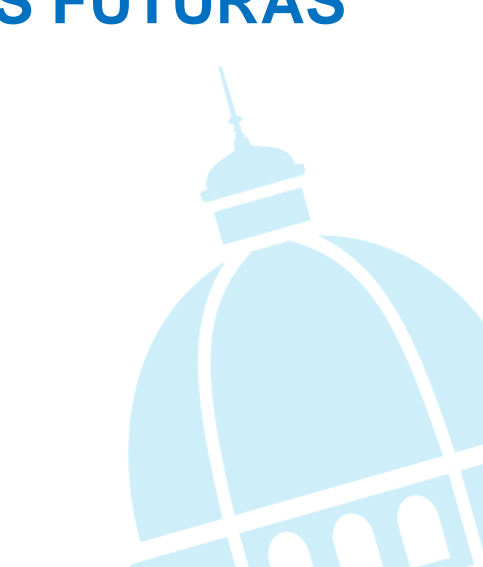
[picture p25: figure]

CONSTRUCCIÓN Y CONTROL DE UN ROBOT CONTINUO DE CABLES CON DISCOS PIVOTANTES

ELENA MUÑOZ SÁNCHEZ | 47

### 7. LINEAS FUTURAS

Gracias a que el Pylori-I se ha construido en la propia Escuela Técnica Superior de Ingenieros Industriales, es fácil que un futuro alumno retome el proyecto y lo mejore.
Para continuar con un buen desarrollo del Pylori-I, se plantean diferentes campos de investigación con los que mejorar el proyecto:
- Materiales de construcción
A la vista de los resultados de los experimentos, queda claro que uno de los principales impedimentos para el correcto movimiento del robot son los materiales con los que está construido.
Una posible solución sería cambiar la impresión 3D de los discos por fabricación en aluminio. De esta manera, podrían emplearse cables de acero para el accionamiento sin riesgo de romper los discos, minimizando el rozamiento que actualmente hay entre disco e hilo, y aportándole una mayor resistencia ante grandes tensiones.
Además, dada la consistencia de esta nueva construcción, se podría prescindir de la malla elástica, proporcionando una mayor visión de los cables.
- Mejora de la IHM
Actualmente, en la interfaz hombre-máquina es posible hacer la conexión con Matlab-Arduino, pero no el envío de datos de uno a otro.
Como mejora a realizar se podría terminar esa fase de la interfaz cuando los experimentos den resultados satisfactorios, ya que ese ha sido el motivo por el cual no se ha realizado hasta ahora este intercambio de información.
- Instalación de una herramienta
En el prototipo actual no se ha instalado ningún tipo de herramienta en el TCP pese a que tanto el banco de motores como el armario eléctrico tienen capacidad para albergar dos motores más.
Como futuro objetivo, cabe la posibilidad de instalar una pinza eléctrica en el extremo para utilizar el robot como un modelo manipulador, o bien una cámara que pueda utilizarse en situaciones de inspección o en entornos relacionados con la medicina.
- Diseñar un método de calibración y automatizar las mediciones en los experimentos
Actualmente, dado que se trata de un primer prototipo, el entorno de trabajo en el que se realizan los experimentos es muy simple y poco preciso, ya que se realizan las medidas de manera manual.
Como futura mejora se contempla la posibilidad de realizar estas medidas mediante el análisis de las imágenes que nos proporcionarían dos webcams instaladas en el espacio de trabajo.
Además de esto, el sistema de calibración se realiza ‘a ojo’ ya que no se tiene un acceso completo a los cables para poder comprobar la tensión a la que están sometidos. Es posible que exista un método que, junto con la utilización de diferentes materiales de construcción, proporcione una calibración fiable y duradera.
- Control mediante joystick o mediante realidad virtual
En el CAR ya se han desarrollado varios proyectos que se han llevado a realidad virtual con éxito. Por tanto, una posible línea futura de investigación seria desarrollar un entorno virtual en el que poder interactuar con el robot o bien, realizar un control del movimiento del robot mediante un joystick.

LÍNEAS FUTURAS

48 | ESCUELA TÉCNICA SUPERIOR DE INGENIEROS INDUSTRIALES (UPM)

Asimismo, dentro de este nuevo desarrollo en realidad virtual, resultaría muy interesante implementar la detección de objetos u obstáculos y la operación con ellos.

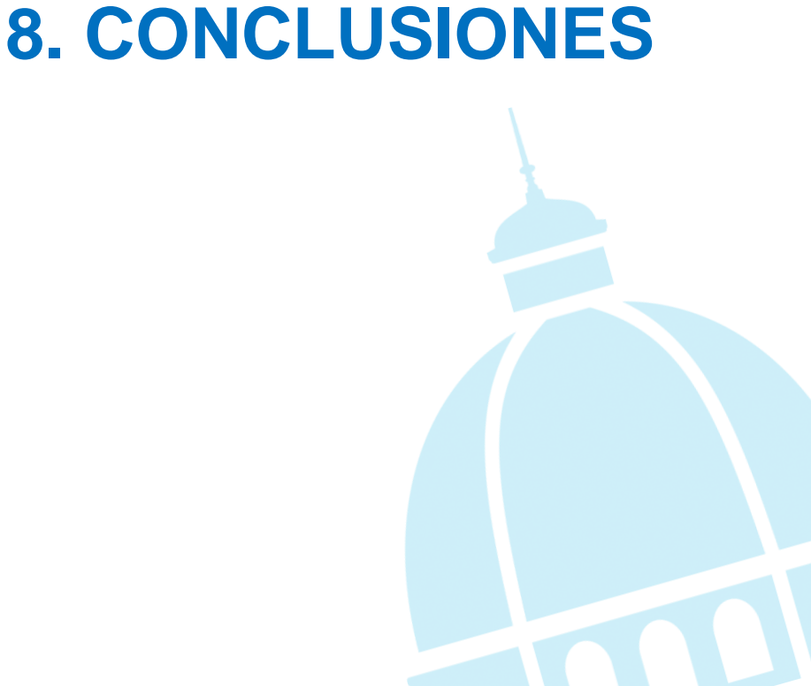
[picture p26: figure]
8. CONCLUSIONES

CONSTRUCCIÓN Y CONTROL DE UN ROBOT CONTINUO DE CABLES CON DISCOS PIVOTANTES

ELENA MUÑOZ SÁNCHEZ | 49

### 8. CONCLUSIONES

Al comienzo de este trabajo se ha realizado un estudio sobre los diferentes tipos y clasificaciones de los robots, así como de su estado del arte. Dicho estudio ha sido gran ayuda a la hora de la elección del prototipo que se iba a diseñar.
Finalmente, se ha decidido realizar un robot híper-redundante, continuo y blando con 16 GdL y construido mediante TPCJ, adecuado para emplearse en áreas de inspección y medicina al que se ha llamado Pylori-I. Por tanto, se desea que el Pylori-I pueda llevar a cabo recolecciones de muestras, tareas de inspección visual y manipulación de objetos de pequeño calibre. Su posible miniaturización también es contemplada de cara a poder introducirse en zonas de difícil acceso o realizar inspecciones médicas más profundas. A partir de dichas características, se han hecho las modificaciones necesarias en el diseño original del prototipo. En el diseño final, la estructura del robot está compuesta por 52 discos pivotantes distribuidos en cuatro secciones de la forma 20-12-12-8 partiendo desde la base. El disco posicionado en el extremo de cada sección tiene que ser diferente de los demás para poder fijar los cables en ellos.
La actuación se realiza mediante cables y motores PaP. La disposición de los cables escogida es de cuatro actuadores por sección que se encuentran diametralmente opuestos dos a dos. En su construcción es muy importante tener en cuenta el desfase que hay entre cada sección para un correcto guiado de los cables.
Está compuesto casi en su totalidad por componentes impresos en 3D, a excepción de los cables, los motores y la malla protectora. Su longitud final es de 260 mm, 463 mm si se tienen en cuenta el distribuidor de cables y el banco de motores.
Dado que se trata de un robot continuo y blando, podrá ser empleado como robot colaborativo en cualquier entorno, incluida la naturaleza, ya que su movimiento continuo semejante al de una serpiente o una trompa de elefante evita grandes impactos ambientales. En cuanto al control cinemático, se ha realizado una comparación entre las cinemáticas ya existentes para este tipo de robot, llegando a la conclusión de que, aquellas que se han implementado utilizando el cálculo de la Jacobiana, no funcionan correctamente una vez se añaden las restricciones de giro de los discos. Por lo tanto, la cinemática utilizada en el proyecto ha sido aquella calculada mediante el Descenso del Gradiente.
Como hardware de control se ha empleado un armario electrónico proporcionado por el CAR y que se compone, principalmente, de un Arduino Due y 18 drivers TB6600. Este armario controla motores de tipo PaP mediante Arduino recibiendo como dato de Matlab los pulsos que han de girar los motores.
Llegados al punto de los experimentos y sus resultados, la principal conclusión es que se observan diferencias entre el comportamiento del robot físico y los obtenidos de manera teórica. Esto puede ser debido a que se ha considerado un comportamiento ideal para el robot en el que la flexión de la sección se distribuye uniformemente a lo largo de todos los discos que la conforman, a la fricción entre cables y discos, o a una mala calibración inicial.
Cabe destacar que el comportamiento del robot no es del todo erróneo ya que se orienta y aproxima hacia el punto deseado, solo que con un error muy superior al indicado en simulación.
Por tanto, como resultado de este primer prototipo realizado en el CAR que emplea TPCJ como método constructivo, hay que resaltar que el Pylori-I posee todas las características buscadas para tener una gran flexibilidad y maniobrabilidad ante obstáculos.

CONCLUSIONES

50 | ESCUELA TÉCNICA SUPERIOR DE INGENIEROS INDUSTRIALES (UPM)

# 9. ENLACES EXTERNOS

CONSTRUCCIÓN Y CONTROL DE UN ROBOT CONTINUO DE CABLES CON DISCOS PIVOTANTES

ELENA MUÑOZ SÁNCHEZ | 51

### 9. ENLACES EXTERNOS

Debido a la gran cantidad de programas, datos, información, imágenes y videos utilizados y generados a lo largo del proyecto, se ha creado un repositorio y una lista de reproducción de acceso público que poder visitar en caso de cualquier duda o de querer tener más información referida a este trabajo.
El repositorio se puede encontrar en el siguiente enlace: https://github.com/LnaMzSz/Pylori-I
La lista de reproducción con los videos realizados se puede encontrar en YouTube mediante el siguiente enlace: https://youtube.com/playlist?list=PL3Q5Xz4yvA3jVhCCdIYIbSSO-qLm97V_n

ENLACES EXTERNOS

52 | ESCUELA TÉCNICA SUPERIOR DE INGENIEROS INDUSTRIALES (UPM)
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

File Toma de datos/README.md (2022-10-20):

# Toma de datos

Esta carpeta contiene el codigo empleado para tomar datos del comportamiento del robot, los .xls con los datos obtenidos y el codigo empleado para el tratamiento de datos.

### Instalacion
Para ejecutar el codigo para la toma de datos en matlab hay que tener instalado ROS (y en concreto el paquete ros_kinetic_vrpn_client_ros) y el add-on ROS Toolbox de Matlab (disponible a patir de Matlab2019).

La version de Ros empleada en este caso ha sido Kinetic, pero deberia valer tambien Melodic sin hacer apenas cambios. 

El ordenador desde el que se transmiten los datos tiene que tener la opcion de transmision de datos mediante VRPN de Optitrack. Es aconsejable revisar la mascara del ordenador que recibe los datos y que ninguno de ellos esta conectado a internet.

### Uso
Los archivos de la toma de datos corresponden cada uno a un experimento diferente y viene indicado en su nombre que motores del robot se mueven en cada uno.

Al principio de estos archivos se establece la conexion con Arduino con un Baudrate de 11520, asi que hay que modificar el puerto y el Baudrate (si fuera necesario) para usarlos.

Despues se inicializa la conexion de ros y se suscribe al topic deseado. Para ello se le pasa a la funcion rosinit la IP del ordenador que transmite los datos y el puerto desde el que lo hace, por lo que habra que modificar los valores para usarlos con otro ordenador.
La funcion receive captura todos los datos que transmite el topic elegido cada vez que se ejecuta pero hay que indicarle que margen de tiempo puede tardar como maximo en recibir un dato antes de dar error. Este valor se puede modificar segun se requiera (aumentarlo puede hacer que se tarde mÃ¡s en tomar los datos pero si la conexion es lenta o la frecuencia de transmision de datos baja, puede ser necesario aumentarlo).

Se usa la funcion writematrix para volcar en un .xls cuyo nombre se debe indicar (funciona con mas formatos) tanto los datos que se quiere guardar como el header para indicar que son (se puede modificar segun resulte mas comodo). Se hace usando append para que siempre coloque los datos nuevos en la linea de debajo de los que ya hay pero existen mas opciones.

Dentro del bucle se mueven los motores y se capturan los datos de su posicion despues de cada mmovimiento. 
Al final se devuelve el robot a su posicion de reposo y se cierra la conexion con Arduino.

El archivo transformador_optitrack.m transforma la orientacion de la posicion del robot que se le pasa a angulos de Euler y encuentra la matriz de transformacion para hacer el cambio de sistema de referencia del del optitrack al del robot (MTH). 
Y el archivo transf_dat.m ejecuta el archivo transformador_optitrack.m con los datos del robot en la posicion de reposo (que se le pasa en la variable ini) y usa la matriz obtenida para transformar todos los datos que se le pasan (en la variable data) y los vuelca en otro .xls.

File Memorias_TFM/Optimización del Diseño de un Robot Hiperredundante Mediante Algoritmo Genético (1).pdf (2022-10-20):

# OPTIMIZACIÓN DEL DISEÑO DE UN ROBOT HIPER - REDUNDANTE DE


# CABLES MEDIANTE ALGORITMO GENÉTICO

SEPTIEMBRE 2021

# JAIME BRAVO ALGABA

DIRECTOR DEL TRABAJO FIN DE GRADO:

## Antonio Barrientos Cruz

## Jaime Bravo Algaba

### TRABAJO FIN DE GRADOPARA LA OBTENCIÓN DEL TÍTULO DE GRADUADO EN INGENIERÍA EN TECNOLOGÍAS INDUSTRIALES

Jaime Bravo Algaba | I

“When you grow up and something touches you emotionally, it lives on forever.”

David Edward Goldberg

Jaime Bravo Algaba | III

## AGRADECIMIENTOS

A mis padres, por haberme dado medios para crecer, consejos para avanzar y fuerza para levantarme.

A mi abuela, por todo lo que habrá podido llegar a rezar para que aprobara Cálculo.

A mi tío, por haber apostado siempre por mí.

Gracias a los Gerardos, por tantos ratos en la multi y, sobre todo, por ser auténticos.

A mi compañera Elena, por haber escuchado mis audios con paciencia...

Agradezco también a mi tutor Antonio por sus consejos y por la implicación que demuestra día a día con los estudiantes.

Y a todos los que me habéis acompañado durante esta etapa de mi vida, con momentos buenos, momentos malos y momentos peores, pero que me ha ayudado a crecer como persona y de la que me llevo gente maravillosa.

Optimización del Diseño de un Robot Hrr. de Cables Mediante A. G.


Jaime Bravo Algaba | V
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

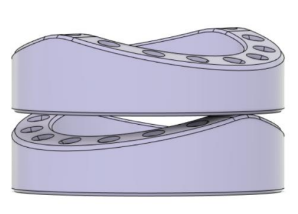
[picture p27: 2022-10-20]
Images/diseño_2_discos.png

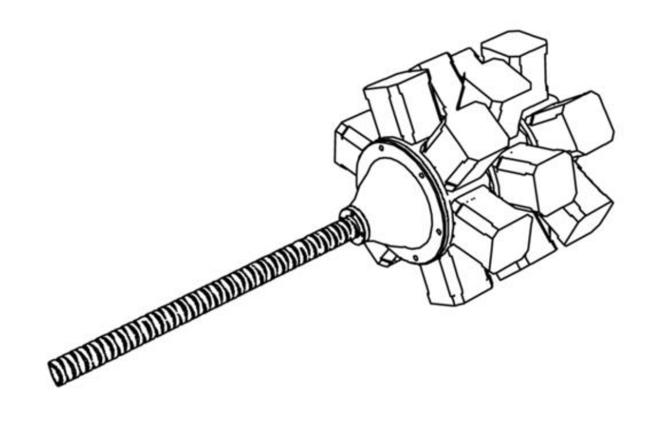
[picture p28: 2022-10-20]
Images/Diseño_pylori.png

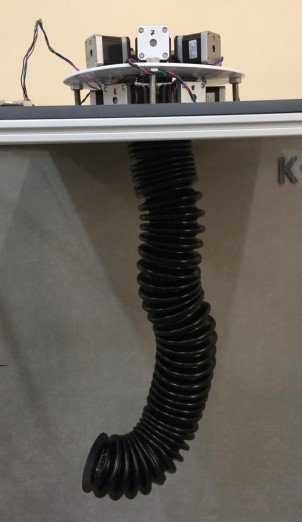
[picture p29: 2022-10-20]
Images/kyma.jpg

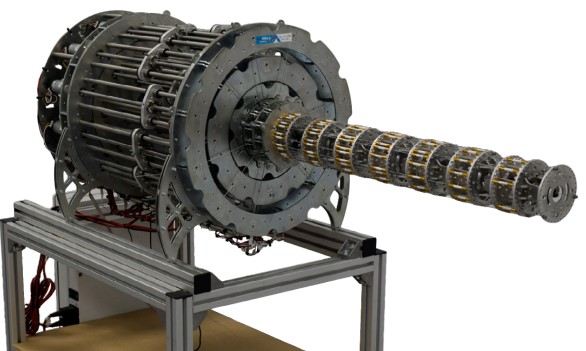
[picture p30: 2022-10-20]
Images/mach.jpg

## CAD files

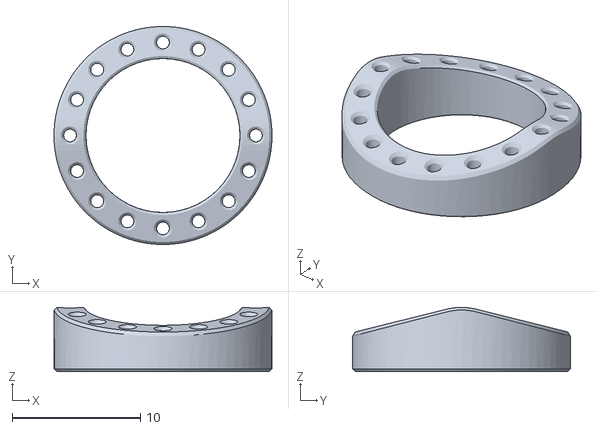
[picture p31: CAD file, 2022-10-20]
piezas_STL/100pcs_Seccion.stl
17.0 x 17.0 x 5.00

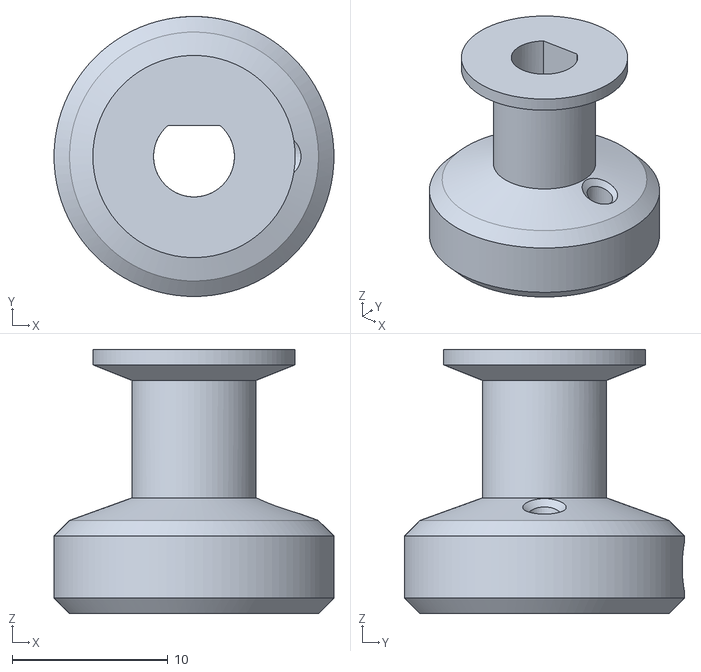
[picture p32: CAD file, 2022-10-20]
piezas_STL/polea_eje_en_D v4.stl
18.0 x 18.0 x 17.0

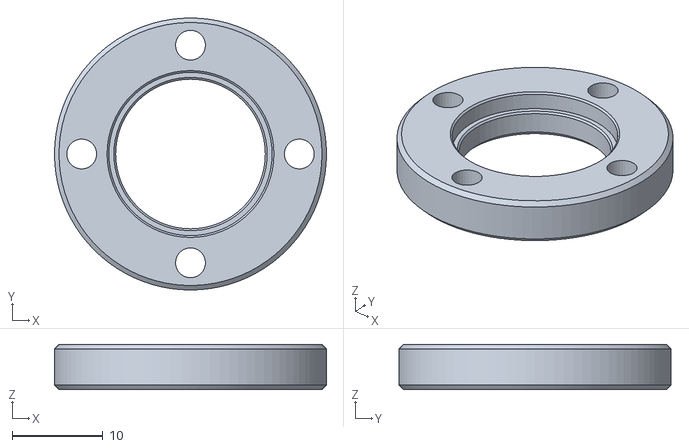
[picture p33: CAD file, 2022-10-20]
piezas_STL/1pcs_Robot_Base.stl
30.0 x 30.0 x 5.00

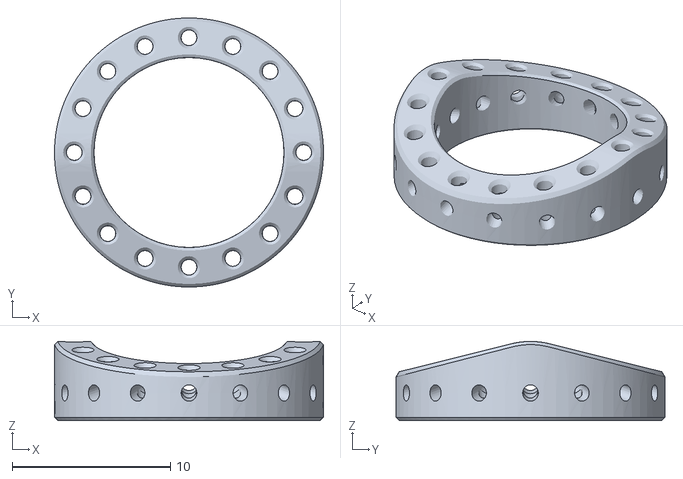
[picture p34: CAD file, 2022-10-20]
piezas_STL/5pcs_End_Boro.stl
17.0 x 17.0 x 5.00

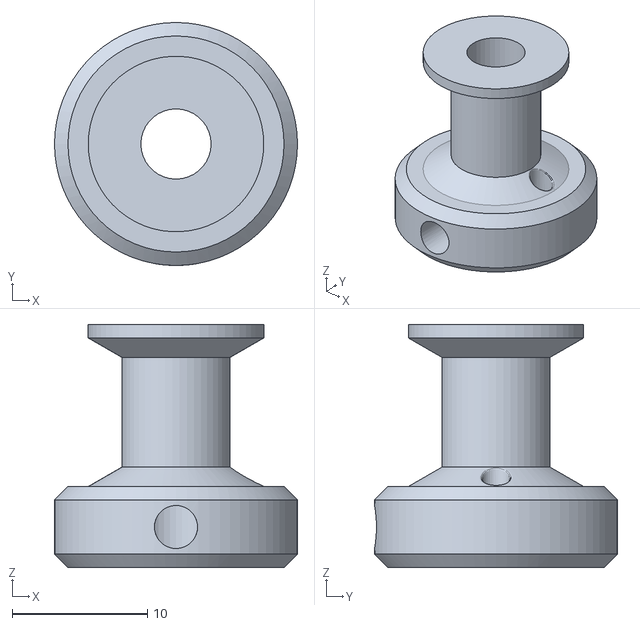
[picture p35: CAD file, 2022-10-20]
piezas_STL/18pcs_Acople_Motor.stl
18.0 x 18.0 x 18.0

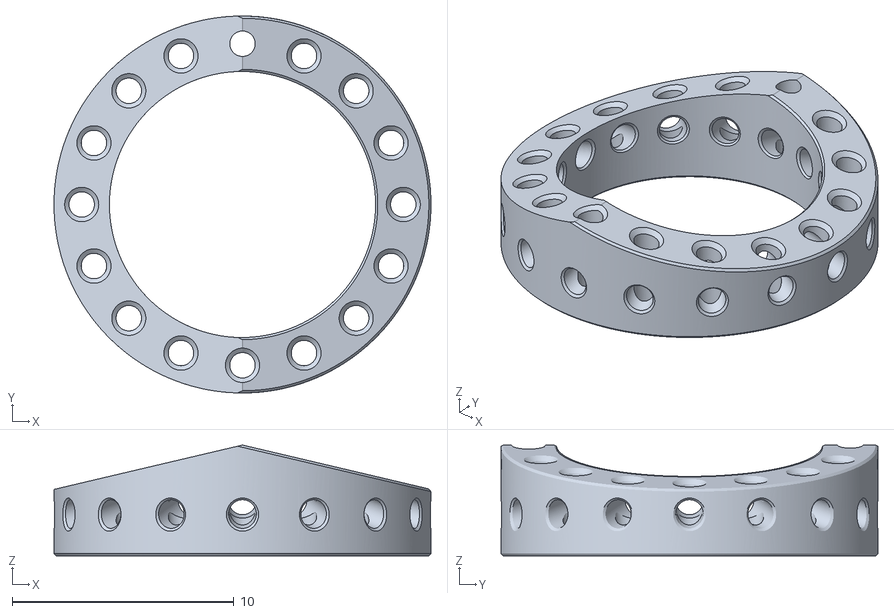
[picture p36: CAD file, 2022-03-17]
piezas_STL/End_Boro_Triang.stl
17.0 x 17.0 x 5.00

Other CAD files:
piezas_STL/Robot_Base.stl

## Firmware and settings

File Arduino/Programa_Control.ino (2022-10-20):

#include <AccelStepper.h>

//200 pulsos/rev ----- microstepping: 1600 pulsos/rev

enum {
  NUM_MOT = 18,
  DIS_MODE = 0,
  SPEED_MODE = 1,
  SERVO_MODE = 2,
  SET_POS = 3
};


const int Motor_Number[] = {1, 2, 3, 4, 5, 6, 7, 8, 9, 10, 11, 12, 13, 14, 15, 16, 17, 18};
const int Pulse_Pins[] = {13, 11, 9, 7, 5, 3, 14, 16, 18, 20, 22, 24, 26, 28, 30, 32, 34, 36};
const int Dir_Pins[] =   {12, 10, 8, 6, 4, 2, 15, 17, 19, 21, 23, 25, 27, 29, 31, 33, 35, 37};
const int Ena_Pins[] =   {48, 48, 48, 49, 49, 49, 50, 50, 50, 51, 51, 51, 52, 52, 52, 53, 53, 53};

int Motor_Mode[NUM_MOT] = {0}; //0 Disabled, 1 Speed Mode, 2 Servo Mode.
bool New_Data[NUM_MOT] = {0}; //0 Disabled, 1 Speed Mode, 2 Servo Mode.
float Motor_Speed[NUM_MOT] = {0};
float Motor_Target_Pos[NUM_MOT] = {0};


String Serial_String;
long timestamp;
AccelStepper *stepper[NUM_MOT] = { NULL };

void setup()
{
  //Serial para comunicación
  Serial.begin(115200);
  //Defino objetos para controlar los motores
  for (int i = 0; i < NUM_MOT; ++i) {
    stepper[i] = new AccelStepper(AccelStepper::DRIVER, Pulse_Pins[i], Dir_Pins[i]);
  }

  //Configuracion de movimiento para los motores
  for (int i = 0; i < NUM_MOT; ++i) {
    stepper[i]->setMaxSpeed(6000); // 100mm/s @ 80 steps/mm
    stepper[i]->setPinsInverted (false, true, true);//DIR,STEP,ENABLE
    stepper[i]->setEnablePin(Ena_Pins[i]);
    stepper[i]->enableOutputs();
    stepper[i]->setSpeed(0);
  }
}

void loop()
{
  readSerial();
  setConfig();

  //*********************Sentencias para movimiento****************//
  for (int i = 0; i < NUM_MOT; ++i) {
    if (Motor_Mode[i] == SPEED_MODE) {
      stepper[i]->runSpeed();
    }
    else if (Motor_Mode[i] == SERVO_MODE) {
      stepper[i]->runSpeedToPosition();
    }
  }
  //**************************************************************//

}


void setConfig() {
  for (int i = 0; i < NUM_MOT; ++i) {
    if (New_Data[i]) {
      stepper[i]->moveTo(Motor_Target_Pos[i]);
      stepper[i]->setSpeed(Motor_Speed[i]);
      Serial.println("Motor: ");
      Serial.print(i);
      Serial.print(" ---- Posicion: ");
      Serial.print(Motor_Target_Pos[i]);
      Serial.print(" ---- Velocidad: ");
      Serial.print(Motor_Speed[i]);
      Serial.println('\n');
      
      New_Data[i] = false;
    }
  }
}

void readSerial() {
  if (Serial.available()) {
    timestamp = millis();
    Serial_String = Serial.readStringUntil('\n');
    Serial.println(Serial_String);
    Serial_String.trim();
    if (Serial_String.startsWith("[") && Serial_String.endsWith("]")) {
      Serial_String = Serial_String.substring(1, Serial_String.length() - 1);
      char c_arr[100] = {};
      Serial_String.toCharArray(c_arr, Serial_String.length());

      /* get the first token */
      char *token = strtok(c_arr, ";");
      float arg_data[4] = {0};
      int index = 0;
      /* walk through other tokens */
      while ( token != NULL ) {
        arg_data[index] = atof(token);
        ++index;
        token = strtok(NULL, ";");
      }
      New_Data[(int)arg_data[0] - 1] = true;
      Motor_Mode[(int)arg_data[0] - 1] = arg_data[1];

      switch (Motor_Mode[(int)arg_data[0] - 1] ) {
        case DIS_MODE: //Disable
          Motor_Speed[(int)arg_data[0] - 1] = 0;
          Motor_Target_Pos[(int)arg_data[0] - 1] = 0;
          stepper[(int)arg_data[0] - 1]->disableOutputs();
          break;
        case SPEED_MODE: //Speed mode
          Motor_Speed[(int)arg_data[0] - 1] = arg_data[2];
          stepper[(int)arg_data[0] - 1]->enableOutputs();
          break;
        case SERVO_MODE: //Servo mode
          Motor_Speed[(int)arg_data[0] - 1] = arg_data[2];
          Motor_Target_Pos[(int)arg_data[0] - 1] = arg_data[3];
          stepper[(int)arg_data[0] - 1]->enableOutputs();
          break;
        case SET_POS: //Set Position
          stepper[(int)arg_data[0] - 1]->setCurrentPosition(arg_data[2]);
          New_Data[(int)arg_data[0] - 1] = false;
          break;
        default:
          New_Data[(int)arg_data[0] - 1] = false;
          Serial.println("Comando no admitido");
          break;
      }
    }
    else {
      Serial.println("Formato de mensaje incorrecto");
    }

  }
}

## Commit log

2022-05-18 Fix stl file names
2022-06-02 se añade una función que es capaz de mover cualquier motor durante unos segundos y luego lo para
2022-06-02 Se añaden la función calibrarRobot que permite establecer la posición actual del robot o de un motor como la 0 o llevar el robot a su posición 0; y la función moverRobot que debería comprobar si es u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
2022-06-03 Se ha añadido una línea para limpiar el serial de arduino antes de empezar a la función mover_motor
2022-06-10 Se han comentado todas las líneas para establecer y cerrar la conexión con arduino, para que al abrir y cerrar la conexión no borre la configuración de donde estaba el origen y presuponga por defecto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
2022-06-10 Demo ha pasado de ser un script a ser una función para poder cambiar a que punto se manda el robot sin tener que reescribir nada en Demo.
2022-06-16 Se incluye en el Readme el proposito del proyecto, los requisitos para ejecutarlo y las instrucciones de uso
2022-06-24 Se añade un script para simular trayectorias de circulo
2022-06-24 Ahora se simula un circulo entero en planos XY, en vez de solo un semicírculo
2022-07-03 arreglado código para destensar motores primero
2022-07-04 Se vuelve a añadir el archivo correcto de Robot_Base.stl y se multiplican los pulsos por 3 antes de moverlos en moverRobot porque se ha visto que funcionaba con otra version.
    [Robot_Base.stl]
2022-08-09 Se añaden scripts para transformar los datos obtenidos mmediante el optitrack de modo que tengan como eje de coordenadas la base del robot
2022-08-09 Se implementa la red neuronal de cinemática inversa (para un espacio de 2x2cm) con los pesos y sesgos importados de python en el script nn, y se añade la funcion reescalado_nn que reescala los datos 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
2022-08-09 Se escriben scripts de prueba (no se han escrito para que sean eficientes) para comprobar si la red neuronal funciona correctamente intentando trazar un círculo centrado en el origen y con 1.5 cm de 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
2022-08-09 Se modifican las fucniones mover_motor, moverRobot y long2pulsos para que permitan mover el robot a partir de los pulsos que devuelve la red neuronal y no del alargamiento de los hilos y la configura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
2022-09-29 readme de la carpeta del código de toma de datos
2022-09-29 se crea carpeta con los archivos stl
    [End_Boro_Triang.stl, Robot_Base.stl]
2022-09-29 se añaden los .stl que faltaban
    [100pcs_Seccion.stl, 18pcs_Acople_Motor.stl, 1pcs_Robot_Base.stl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]
2022-09-30 Se añaden las memorias de los TFM y TFG del proyecto
2022-09-30 Se añade la carpeta con el código para entrenar y usar la red neuronal
    [full_data.csv]
2022-12-22 he puesto hello world en el readme
2022-12-22 he añadido una exclamacion en el readme
